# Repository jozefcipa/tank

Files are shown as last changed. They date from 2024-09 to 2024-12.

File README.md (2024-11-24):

# Tank

> A simple robot vehicle built on Arduino and controlled via Bluetooth

<!-- TODO: Replace with a better photo -->
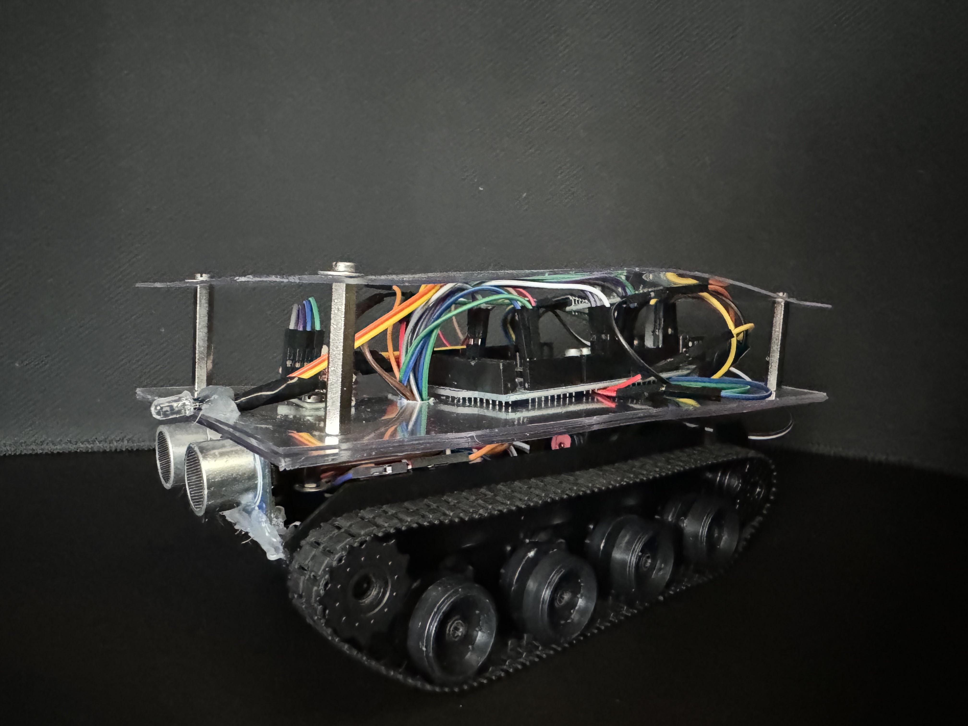
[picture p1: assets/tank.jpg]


This tank is built on Arduino MEGA 2560 using [PlatformIO](https://platformio.org/).
It is equipped with several sensors and a bluetooth module, so it can be controlled remotely via a web app.

## Control app

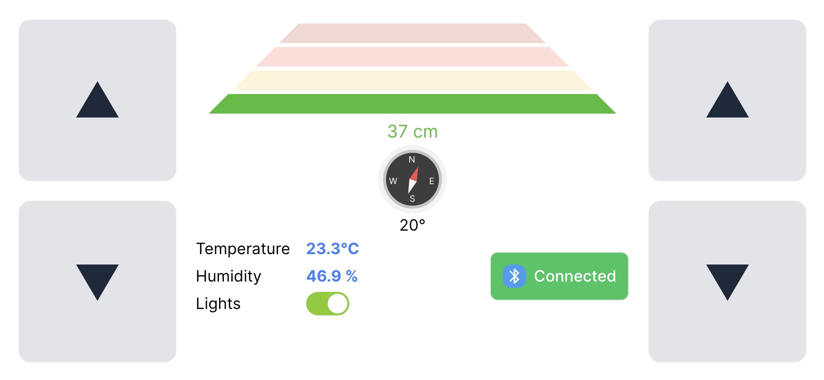
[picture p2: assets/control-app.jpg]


The control app is a regular web application written in React.js and uses [Web Bluetooth API](https://developer.mozilla.org/en-US/docs/Web/API/Web_Bluetooth_API) for connecting and communicating with the bluetooth module of the tank.

Once the connection is established, you can read sensor values from the board and also control the tank movement with the buttons.

[Github repository](https://github.com/jozefcipa/tank-app)

## Sensors
This tank is equipped with several sensors to measure the surrounding environment.
Here's the block diagram of the whole board.

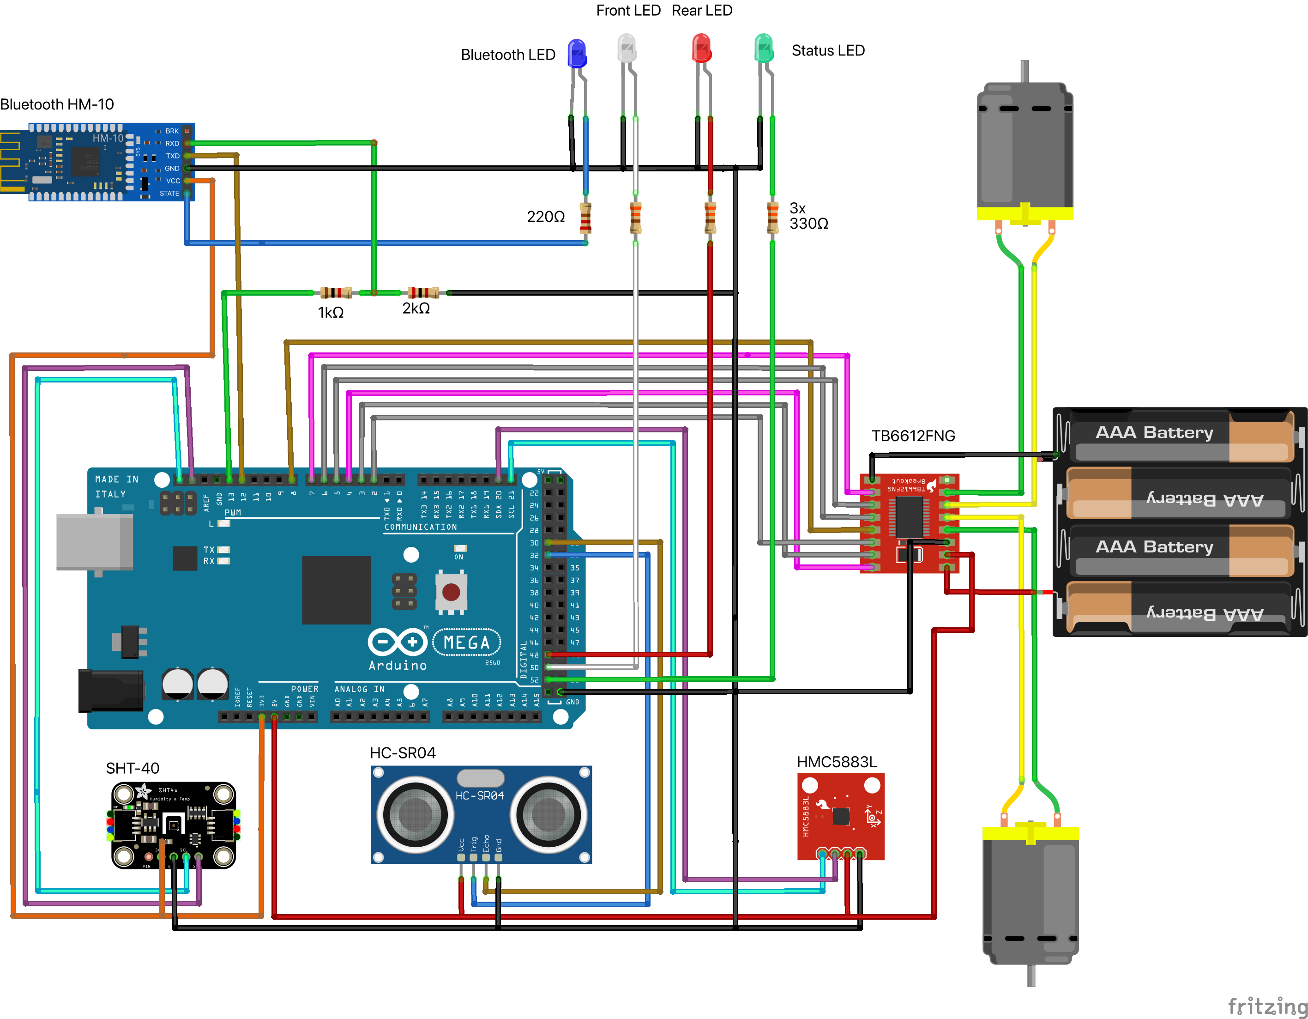
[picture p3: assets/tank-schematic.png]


### Sonar

Distance measuring is possible thanks to the [HC-SR04](https://www.laskakit.cz/arduino-ultrazvukovy-meric-vzdalenosti-hc-sr04/) ultrasonic sensor.

| HC-SR04 sonar | Arduino |
| --- | --- |
| Trigger | D32 |
| Echo | D30 |
| GND | GND |
| VCC | 5V |

### Compass

For direction detection the robot uses the [HMC5883L](https://www.laskakit.cz/3-osy-magnetometr-a-kompas-hmc5883l/) compass which uses the I2C communication protocol.

| HMC5883L compass | Arduino |
| --- | --- |
| SCL | SCL |
| SDA | SDA |
| GND | GND |
| VCC | 5V |

### Thermometer

Measuring temperature and humidity is handled by the [SHT-40](https://www.laskakit.cz/laskakit-sht40-senzor-teploty-a-vlhkosti-vzduchu/) sensor which uses the I2C communication protocol.

| SHT-40 thermometer | Arduino |
| --- | --- |
| SCL | SCL |
| SDA | SDA |
| GND | GND |
| VCC | 3.3V |

### Motors

This robot uses two DC motors that are integrated into the [tank chassis](https://www.laskakit.cz/roboticky-podvozek-pasovy-plastovy/) and uses the [TB6612FNG](https://www.laskakit.cz/dvoumotorovy-radic-tb6612fng/)  driver for controlling the motors.

| TB6612FNG motors driver | Arduino |
| --- | --- |
| AIN1 | D2 |
| AIN2 | D3 |
| PWMA | D4 |
| BIN1 | D6 |
| PWMB | D7 |
| STBY | D8 |
| GND | GND |
| VCC | 5V |

## Bluetooth

This tank uses the [HM-10](https://www.laskakit.cz/huamao-hm-10c-a-orig--bluetooth-v4-0-ble-modul-cc254x/) Bluetooth 4.0 module which supports Bluetooth Low Energy (BLE) and thus can be used for connecting to the controling app running in a browser.

| HM-10 Bluetooth | Arduino | Notes |
| --- | --- | --- |
| RX | D13 | Connected via a voltage divider. See the diagram below. |
| TX | D12 |  |
| STATE | - | Connected to the blue LED through a 220R resistor |
| VCC | 3.3V |  |
| GND | GND |  |

When connecting with Arduino, we need to add a voltage divider between RX pin of the bluetooth module and TX pin of the Arduino board, as they are working on different voltage levels (5V vs. 3.3V).
The electric circuit can be seen on the diagram above.

## LEDs

The robot uses the following LEDs for different purposes. <br>
There is white (FRONT) and red (REAR) LED that serve as lights.<br>
Once the program is loaded and everything is initialized, the green LED (STATUS) will blink at the beginning of each loop.<br>
 Lastly, we have the blue LED (BLUETOOTH) that turns on once the Bluetooth connection with the controlling app is established.

| LED | Arduino | Notes |
| --- | --- | --- |
| STATUS | D52 | Through a 330R resistor |
| FRONT | D50 | Through a 330R resistor |
| REAR | D48 | Through a 330R resistor |
| BLUETOOTH | - | Connected to the BT module, through a 220R resistor  |

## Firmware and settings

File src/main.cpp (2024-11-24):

/**
* Bluetooth controlled Tank vehicle
**/
#include <Arduino.h>
#include <Wire.h>
#include <string.h>
#include "leds/leds.h"
#include "bluetooth/bluetooth.h"
#include "tank/tank.h"

char *bluetoothMessage;

void setup() {
  // Configure console
  Serial.begin(9600);
  Serial.println("Tank initializing...");
  tank::setup();
  Serial.println("Tank initialization is complete.");
}

void loop() {
  led::blinkStatusLed();

  // We need to save the string message first, in order to keep the c_str() reference valid
  // See https://gcc.gnu.org/onlinedocs/gcc/Temporaries.html
  String message = bluetooth::read();
  bluetoothMessage = (char *) message.c_str();
  if (strcmp(bluetoothMessage, "") == 0) {
    if (tank::shouldStopMotors()) {
      tank::stopMotors();
    }

    delay(50);
    return;
  }

  // Parse bluetooth message
  Serial.print("[Bluetooth]: Received message: ");
  Serial.println(bluetoothMessage);
  tank::Command command = tank::parseMessage(bluetoothMessage);

  // Handle motors
  if (command.motors != NULL) {
    tank::handleMotors(command.motors);
  }

  // Handle lights
  if (command.lights != NULL) {
    tank::handleLEDLights(command.lights);
  }

  // Handle sensors data
  if (command.sensors != NULL) {
    tank::handleSensors(command.sensors);
  }
}

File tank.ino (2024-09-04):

/**
* Bluetooth controlled Tank vehicle
**/

#include <Wire.h>
#include "thermometer.h"

void setup() {
  // Configure console
  Serial.begin(9600);
  Serial.println("Tank initializing...");

  // Setup peripheries
  LED_setup();
  SONAR_setup();

  // Initialize I2C communication
  Wire.begin();
  COMPASS_setup();
  THERMOMETER_setup();

  // Initialize bluetooth at the end, when everything is ready
  BLUETOOTH_setup();

  Serial.println("Tank initialization is complete.");
}

void loop() {
  Serial.print("Distance: ");
  Serial.print(SONAR_readDistance());
  Serial.println("cm");
  Serial.print("Compass: ");
  Serial.print(COMPASS_read());
  Serial.println("°");
  Serial.print("Temperature: ");
  struct TemperatureHumidity temp;
  temp = THERMOMETER_read();
  Serial.print(temp.temperature);
  Serial.print("°C Humidity: ");
  Serial.print(temp.humidity);
  Serial.println("%");
  Serial.println("-----------------");

  String response = _BLUETOOTH_read();

  if (response != "") {
    Serial.println("Response from bluetooth");
    Serial.println(response);

    if (response.equals("on")) {
     LED_turnOnLights();
    } else if (response.equals("off")) {
      LED_turnOffLights();
    } else {
      Serial.println("Unknown command: " + response);
    }

    BLUETOOTH_send("OK");
  }

  delay(1000);
  LED_blinkStatusLed();
}

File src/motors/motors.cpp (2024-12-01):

#include <Arduino.h>
// https://learn.sparkfun.com/tutorials/tb6612fng-hookup-guide/all
#include <SparkFun_TB6612.h>

namespace motors {
  // Right motor
  const int AIN1 = 2;
  const int AIN2 = 3;
  const int PWMA = 4;
  // Left motor
  const int BIN1 = 5;
  const int BIN2 = 6;
  const int PWMB = 7;
  const int STBY = 8;
  const int offsetA = 1;
  // this motor has swapped wires (and I was lazy to fix them),
  // so we can use -1 to reverse direction
  const int offsetB = -1;
  const int SPEED = 150; // PWM value 1-255

  Motor rightMotor = Motor(AIN1, AIN2, PWMA, offsetA, STBY);
  Motor leftMotor = Motor(BIN1, BIN2, PWMB, offsetB, STBY);

  Motor* getMotor(char motorId) {
    switch (motorId) {
      case 'R': return &rightMotor;
      case 'L': return &leftMotor;
      default:
        Serial.println("[motors]: Unknown motor: " + motorId);
        return NULL;
    }
  }

  void stop(char motorId) {
    Motor* motor = getMotor(motorId);
    
    if (motor == NULL) {
      return;
    }

    motor->brake();
  }

  void driveInDirection(char motorId, char direction, int speed) {
    Motor* motor = getMotor(motorId);
    
    if (motor == NULL) {
      return;
    }

    switch (direction) {
      case 'F':
        motor->drive(speed);
        break;
      case 'B':
        motor->drive(-speed);
        break;
      case '0':
        // do nothing, motor should be stopped
        break;
      default:
        Serial.println("[motors]: Unknown direction: " + direction);
        return;
    }
  }
  
  void drive(char motorA, char directionA, char motorB, char directionB) {
    // First stop the motors
    // stop(motorA);
    // stop(motorB);

    // we start the motors gradually using PWM
    for (int currentSpeed = 0; currentSpeed < SPEED; currentSpeed += 10) {
      driveInDirection(motorA, directionA, currentSpeed);
      driveInDirection(motorB, directionB, currentSpeed);
      delay(10);
    }
  }
}

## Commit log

2024-09-04 feat: init Arduino and sonar
2024-09-04 feat: add LEDs
2024-09-11 fix: send lights as separate periphery in message
    [main.cpp]
2024-10-11 fix: update compass angle calculation
    [compass.cpp]
2024-10-17 feat: bug fixes and improvements
    [main.cpp, motors.cpp, tank.cpp]
2024-11-16 wip: motors
2024-11-22 feat: motors setup
2024-11-23 chore: update diagram
    [tank-schematic.fzz]
2024-11-24 feat: control motors via bluetooth
2024-12-01 fix: drive motors with PWM for smooth start
    [motors.cpp, tank.cpp]
